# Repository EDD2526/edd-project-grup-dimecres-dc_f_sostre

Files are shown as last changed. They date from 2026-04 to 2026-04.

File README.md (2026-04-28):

# Projecte Eines Sostre Solar 

>**Autors: Nabel Khrourouch i Marc Baillo** 
>**Versió: 0.2 **

----------

## Objectiu

Dissenyar i implementar en una PCB, un sistema electronic del vehicle com es un sostre solar. S’implementara una etapa de regulacio, microcontrolador,  bus CAN, I2C / SPI, USART i botons. 
I que incloguiu les següents caracteristiques:
- Motor del vidre amb el seu final de carrera. 
- Motor de la cortineta.
- Llums ambientals (LED RGB amb bus digital)
- Mecanisme antiatrapament (sensor digital de corrent).

## Diagrama de blocs

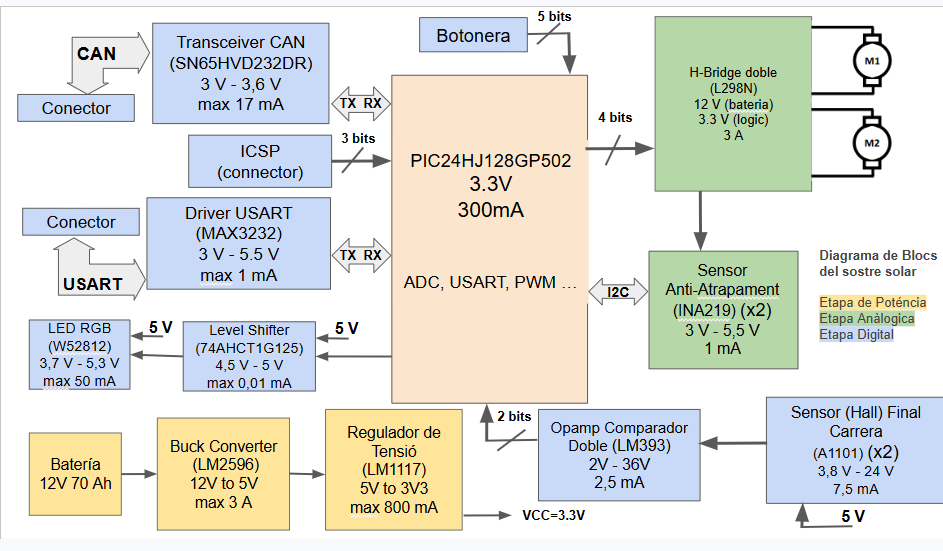
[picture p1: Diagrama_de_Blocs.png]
Diagrama de Bloc


### Descripció/funcionalitat de cada bloc

  * Power: En aquest bloc posem la partt relacionada con 2 etapes, la de la alimentació i la de potencia. (LDO y Buck converter i el H-Bridge)
  * Microcontrolador: en aquest bloc posem les parts que tenen molt que veure amb el microcontrolador com cristal oscilador, ICSP, botonera, filtre pi, reset manual, LEDs de prova.
  * Analógica: part del sistema que és analogic i per tant la agrupem, aquí veiem el sensor de anti-atrapament.
  * Digital: part on están els components més purament digitals, como el USART, el transceiver CAN, el Sensor de Final de Carrera o LED RGB. 

-----------

## Requisits / Especificacions

  * Alimentació; 12V, regulada a 3V3
  * Microcontrolador PIC24hj128gp502
  * Motor del vidre amb el seu final de carrera. 
  * Motor de la cortineta.
  * Llums ambientals (LED RGB amb bus digital)
  * Mecanisme antiatrapament (sensor digital de corrent).

-----------

## Components

| Descripció | Ref | Package | Datasheet | Proveïdor | Preu (per u) | Unitats |
|---|---|---|---|---|---|---|
| Microcontrolador | PIC24HJ128GP502 | TQFP-44 | [Datasheet](https://ww1.microchip.com/downloads/aemDocuments/documents/OTH/ProductDocuments/DataSheets/70293G.pdf) | [Mouser](https://www.mouser.es/ProductDetail/Microchip-Technology/PIC24HJ128GP504-E-PT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) | 6,85€ | 1x |
| Regulador de Tensió | LM1117 | SOT-223 / TO-252-3 | [Datasheet](https://www.ti.com/lit/ds/symlink/lm1117.pdf) | [Mouser](https://www.mouser.es/ProductDetail/Texas-Instruments/LM1117IMPX-3.3-NOPB?qs=X1J7HmVL2ZG7K12CpArCeA%3D%3D) | 0,89€ | 1x |
| Buck Converter (DC/DC) | LM2596 | TO-220-5 | [Datasheet](https://www.onsemi.com/pdf/datasheet/lm2596-d.pdf) | [Mouser](https://www.mouser.es/ProductDetail/onsemi/LM2596DSADJG?qs=atIEnC%2F2K4W1Dy%252BFjrRjIQ%3D%3D) | 2€ | 1x |
| H-Bridge (Doble) | L298N | Multiwatt-15 | [Datasheet](https://www.st.com/resource/en/datasheet/l298.pdf) | [Mouser](https://www.mouser.es/ProductDetail/STMicroelectronics/L298N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) | 9,94€ | 1x |
| Transceiver CAN | SN65HVD232DR | SOIC-8 | [Datasheet](https://www.ti.com/lit/ds/symlink/sn65hvd230.pdf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) | [Mouser](https://eu.mouser.com/ProductDetail/Texas-Instruments/SN65HVD232DR?qs=QViXGNcIEAtY%252BrViRMr46w%3D%3D) | 1,87€  | 1x |
| Driver USART | MAX3232 | SSOP-16 | [Datasheet](https://www.mouser.es/datasheet/3/1014/1/MAX3222-MAX3241.pdf) | [Mouser](https://www.mouser.es/ProductDetail/Analog-Devices-Maxim-Integrated/MAX3232CUE%2bT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) | 6,99€ | 1x |
| Conector | DE9 | DSUB-9_Socket | [Datasheet](https://www.te.com/commerce/DocumentDelivery/DDEController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) | [Mouser](https://www.mouser.es/ProductDetail/TE-Connectivity-AMP/2301843-1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) | 1,9€ | 2x |
| Conector (Batería i Motors) | 282837-2 | THT | [Datasheet](https://www.te.com/commerce/DocumentDelivery/DDEController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) | [Mouser](https://www.mouser.es/ProductDetail/TE-Connectivity/3-282837-2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) | 9,38€ | 3x |
| Sensor (corrent) Anti-Atrapament | INA219 | SOIC-8 | [Datasheet](https://www.ti.com/lit/ds/symlink/ina219.pdf) | [Mouser](https://www.mouser.es/ProductDetail/) | 4,23€ | 2x |
| Sensor Final de Carrera | A1101 | SOT-23 | [Datasheet](https://www.allegromicro.com/~/media/files/datasheets/a110x-datasheet.pdf) | [Mouser](https://www.mouser.es/ProductDetail/Allegro-MicroSystems/A1101EUA-T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) | 1,18€ | 2x |
| Opamp Doble Comparador | LM393 | SOIC-8 | [Datasheet](https://www.ti.com/lit/ds/symlink/lm2903b.pdf?ts=1774335179874&ref_url=https%253A%252F%252Fwww.mouser.pl%252F) | [Mouser](https://www.mouser.es/ProductDetail/Texas-Instruments/LM393AP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) | 0,31 | 1x |
| Cristal Oscilador | ECS-80-20-20BM-EN-TR | 7mm x 5mm | [Datasheet](https://www.mouser.es/datasheet/3/294/1/csm_8mr.pdf) | [Mouser](https://www.mouser.es/ProductDetail/ECS/ECS-80-20-20BM-EN-TR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) | 0,86€ | 1x |
| Ferrita | BLM21 | 0805 | [Datasheet](https://www.mouser.es/datasheet/3/76/1/ENFA0005.pdf) | [Mouser](https://www.mouser.es/ProductDetail/Murata-Electronics/BLM21PG600SN1D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) | 0,10€ | 1x |
| Switch (Pulsador) Reset y Botonera | B3F-1002 | THT | [Datasheet](https://www.mouser.es/datasheet/3/39/1/en_b3f.pdf) | [Mouser](https://www.mouser.es/ProductDetail/Omron-Electronics/B3F-1002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) | 0,27€ | 6x |
| LED blau | LTST-C170TBKT | LED_SMD | [Datasheet](https://www.mouser.com/catalog/specsheets/Lite-On-LTST-C170TBKT.pdf) | [Mouser](https://www.mouser.es/ProductDetail/LITEON/LTST-C170TBKT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) | 0,23€ | 1x |
| LED vermell | LTST-C170KRKT | LED_SMD | [Datasheet](https://www.mouser.com/catalog/specsheets/Lite-On-LTST-C170KRKT.pdf) | [Mouser](https://www.mouser.es/ProductDetail/LITEON/LTST-C170KRKT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) | 0,14€ | 1x |
| LED RGB | WS2812 | LED_SMD | [Datasheet](https://www.tme.eu/Document/01c0100fee68667af99767edc3a7fee2/WS2812B-MINI.pdf) | [TME](https://www.tme.eu/es/details/ws2812b-mini/leds-smd-de-colores/worldsemi/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) | 0,42€ | 1x |
| Level shifter (buffer) | 74AHCT1G125 | SOT-553 | [Datasheet](https://www.ti.com/lit/ds/symlink/sn74ahct1g125.pdf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) | [Mouser](https://www.mouser.es/ProductDetail/Texas-Instruments/74AHCT1G125DBVTG4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) | 0,93€ | 1x |

-----------

## Historial de canvis

| Data | Autor | Branch | Versió | Descripció |
|---|---|---|---|---|
| 10/03/26 | Nabel i Marc | Master | versió 1 | Seleccionem els components i creem la primera versió del Diagrama de Bloc |
| 14/03/26 | Nabel | Master | versió 2 | Actualització del Diagrama de Bloc |
| 16/03/26 | Marc | Master | versió 1 | Esquemàtic: creació dels subapartats del projecte |
| 17/03/26 | Marc | Master | versió 2 | Esquemàtic: faig la part del uC i de Digital |
| 17/03/26 | Nabel | Master | versió 3 | Esquemàtic: faig la part de power i analògica |
| 22/03/26 | Marc | Master | versió 4 | Esquemàtic: correcció d’errades i assignació de footprints |
| 24/03/26 | Nabel | Master | versió 1 | Layout: faig el rutejat de la majoria dels components |
| 24/03/26 | Marc | Master | versió 2 | Layout: corregeixo algunes coses |
| 30/03/26 | Nabel | Master | versió 3 | Layout: rutejat part Digital |
| 31/03/26 | Marc | Master | versió 4 | Layout: treballo part potencia, H_Bridge |
| 08/04/26 | Marc i Nabel | Master | versió 5 | Layout: treballem a classe i l'intentem posar a punt |
| 15/04/26 | Marc i Nabel | Master | versió 6 | Layout: corregim algunes coses com tema de plans i posar plans de massa digital i power |
| 27/04/26 | Nabel | Master | versió 1 | Faig el pressupost |
| 28/04/26 | Marc | Master | versió 7 | Layout: acabo el Layout posant uns canvis proposats pel professor |

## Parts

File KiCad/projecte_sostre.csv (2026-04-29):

Reference | Qty | Value | DNP | Exclude from BOM | Exclude from Board | Footprint | Datasheet
C1,C2,C3,C7,C8,C9,C11,C12,C13,C18,C19,C20,C21,C22,C23,C24,C25,C26,C27,C28,C29,C30,C31,C32,C33,C34,C35,C36,C37,C38 | 30 | 100n |  |  |  | Capacitor_SMD:C_0805_2012Metric | ~
C4,C14,C15,C17 | 4 | 10u |  |  |  | Capacitor_SMD:C_0805_2012Metric | ~
C5,C6 | 2 | 30p |  |  |  | Capacitor_SMD:C_0805_2012Metric | ~
C10 | 1 | 1u |  |  |  | Capacitor_SMD:C_0805_2012Metric | ~
C16 | 1 | 220u |  |  |  | Capacitor_SMD:C_0805_2012Metric | ~
D1,D2 | 2 | LED |  |  |  | LED_SMD:LED_0805_2012Metric | ~
D3,D4 | 2 | 1N5822 |  |  |  | Diode_THT:D_DO-201AD_P15.24mm_Horizontal | http://www.vishay.com/docs/88526/1n5820.pdf
D5 | 1 | WS2812B |  |  |  | LED_SMD:LED_WS2812B_PLCC4_5.0x5.0mm_P3.2mm | https://cdn-shop.adafruit.com/datasheets/WS2812B.pdf
D6,D7,D8,D9,D10,D11,D12,D13 | 8 | D |  |  |  | Diode_SMD:D_SMA | ~
FB1 | 1 | FerriteBead |  |  |  | Resistor_SMD:R_0805_2012Metric | ~
J1,J3,J4,J5,J6 | 5 | Conn_01x02 |  |  |  | Connector_PinHeader_2.54mm:PinHeader_1x02_P2.54mm_Vertical | ~
J2 | 1 | Conn_01x05 |  |  |  | Connector_PinHeader_2.54mm:PinHeader_1x05_P2.54mm_Vertical | ~
J7,J8,J9 | 3 | Screw_Terminal_01x02 |  |  |  | TerminalBlock:TerminalBlock_MaiXu_MX126-5.0-02P_1x02_P5.00mm | ~
J10,J11 | 2 | DE9_Pins |  |  |  | Connector_Dsub:DSUB-9_Pins_Horizontal_P2.77x2.54mm_EdgePinOffset9.40mm | ~
L1 | 1 | 33u |  |  |  | Inductor_SMD:L_1210_3225Metric | ~
R1,R4,R5,R6,R7,R8,R11,R12,R14,R21,R24,R26,R28,R31,R33,R39,R40,R41,R42 | 19 | 10k |  |  |  | Resistor_SMD:R_0805_2012Metric | ~
R2 | 1 | 150 |  |  |  | Resistor_SMD:R_0805_2012Metric | ~
R3,R22,R23 | 3 | 60 |  |  |  | Resistor_SMD:R_0805_2012Metric | ~
R9 | 1 | 3,1k |  |  |  | Resistor_SMD:R_0805_2012Metric | ~
R10 | 1 | 1k |  |  |  | Resistor_SMD:R_0805_2012Metric | ~
R13,R15 | 2 | 3.3k |  |  |  | Resistor_SMD:R_0805_2012Metric | ~
R16,R25 | 2 | 20k |  |  |  | Resistor_SMD:R_0805_2012Metric | ~
R17,R18,R19,R20 | 4 | 50 |  |  |  | Resistor_SMD:R_0805_2012Metric | ~
R27,R29,R30,R32 | 4 | 22k |  |  |  | Resistor_SMD:R_0805_2012Metric | ~
R34,R35,R36,R37 | 4 | 220k |  |  |  | Resistor_SMD:R_0805_2012Metric | ~
R38 | 1 | 330 |  |  |  | Resistor_SMD:R_0805_2012Metric | ~
R43 | 1 | 0 |  |  |  | Resistor_SMD:R_0805_2012Metric | ~
Rshunt1,Rshunt2 | 2 | 0.05 |  |  |  | Resistor_SMD:R_0805_2012Metric | ~
SW1,SW2,SW3,SW4,SW5,SW6 | 6 | SW_Push |  |  |  | Button_Switch_THT:SW_PUSH_6mm | ~
TP_3V3,TP_5V0,TP_GND1,TP_GND2,TP_GND3,TP_GNDPWM1,TP_GNDPWM2,TP_GNDPWM3,TP_GNDPWM4,TP_Vbat0 | 10 | TestPoint |  |  |  | TestPoint:TestPoint_Pad_D1.5mm | ~
TP_PWM_M1,TP_PWM_M2,TP_Rshunt1,TP_Rshunt2,TP_SCL0,TP_SDA0 | 6 | TestPoint_2Pole |  |  |  | TestPoint:TestPoint_2Pads_Pitch2.54mm_Drill0.8mm | ~
U1 | 1 | 74AHCT1G125 |  |  |  | Package_TO_SOT_SMD:SOT-23-5_HandSoldering | http://www.ti.com/lit/sg/scyt129e/scyt129e.pdf
U2,U3 | 2 | LM393 |  |  |  | Package_SO:SOIC-8_3.9x4.9mm_P1.27mm | http://www.ti.com/lit/ds/symlink/lm393.pdf
U4 | 1 | PIC24HJ128GP502 |  |  |  | Package_QFP:TQFP-44_10x10mm_P0.8mm | http://ww1.microchip.com/downloads/en/DeviceDoc/30000684B.pdf
U5 | 1 | LM1117DT-3.3 |  |  |  | Package_TO_SOT_SMD:TO-252-3_TabPin2 | http://www.ti.com/lit/ds/symlink/lm1117.pdf
U6 | 1 | LM2596T-5 |  |  |  | Package_TO_SOT_THT:TO-220-5_P3.4x3.7mm_StaggerOdd_Lead3.8mm_Vertical | http://www.ti.com/lit/ds/symlink/lm2596.pdf
U8,U9 | 2 | INA219AxD |  |  |  | Package_SO:SOIC-8_3.9x4.9mm_P1.27mm | http://www.ti.com/lit/ds/symlink/ina219.pdf
U10 | 1 | MCP2561-E-MF |  |  |  | Package_SO:SOIC-8-1EP_3.9x4.9mm_P1.27mm_EP2.29x3mm | http://ww1.microchip.com/downloads/en/DeviceDoc/25167A.pdf
U11 | 1 | MAX3232 |  |  |  | Package_SO:SOIC-16_3.9x9.9mm_P1.27mm | https://datasheets.maximintegrated.com/en/ds/MAX3222-MAX3241.pdf
U12,U13 | 2 | A1101xLH |  |  |  | Package_TO_SOT_SMD:SOT-23W | https://www.allegromicro.com/-/media/files/datasheets/a110x-datasheet.ashx
U14 | 1 | L298P |  |  |  | Package_SO:Infineon_SOIC-20W_7.6x12.8mm_P1.27mm | http://www.st.com/st-web-ui/static/active/en/resource/technical/document/datasheet/CD00000240.pdf
Y1 | 1 | Crystal |  |  |  | Crystal:Crystal_HC52-6mm_Vertical | ~

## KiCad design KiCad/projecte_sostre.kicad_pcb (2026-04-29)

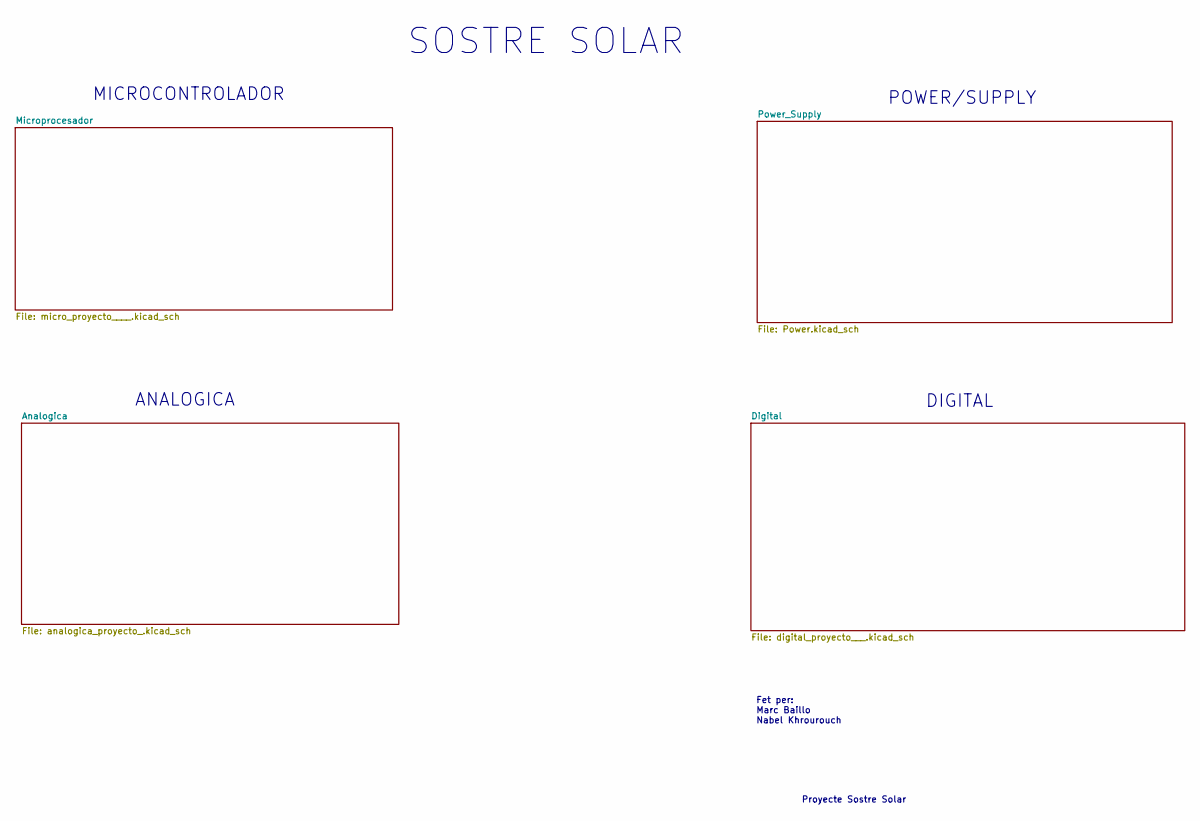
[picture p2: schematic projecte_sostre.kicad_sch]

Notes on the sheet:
SOSTRE SOLAR
Proyecte Sostre Solar
MICROCONTROLADOR
POWER/SUPPLY
ANALOGICA
Fet per: Marc Baillo Nabel Khrourouch
DIGITAL

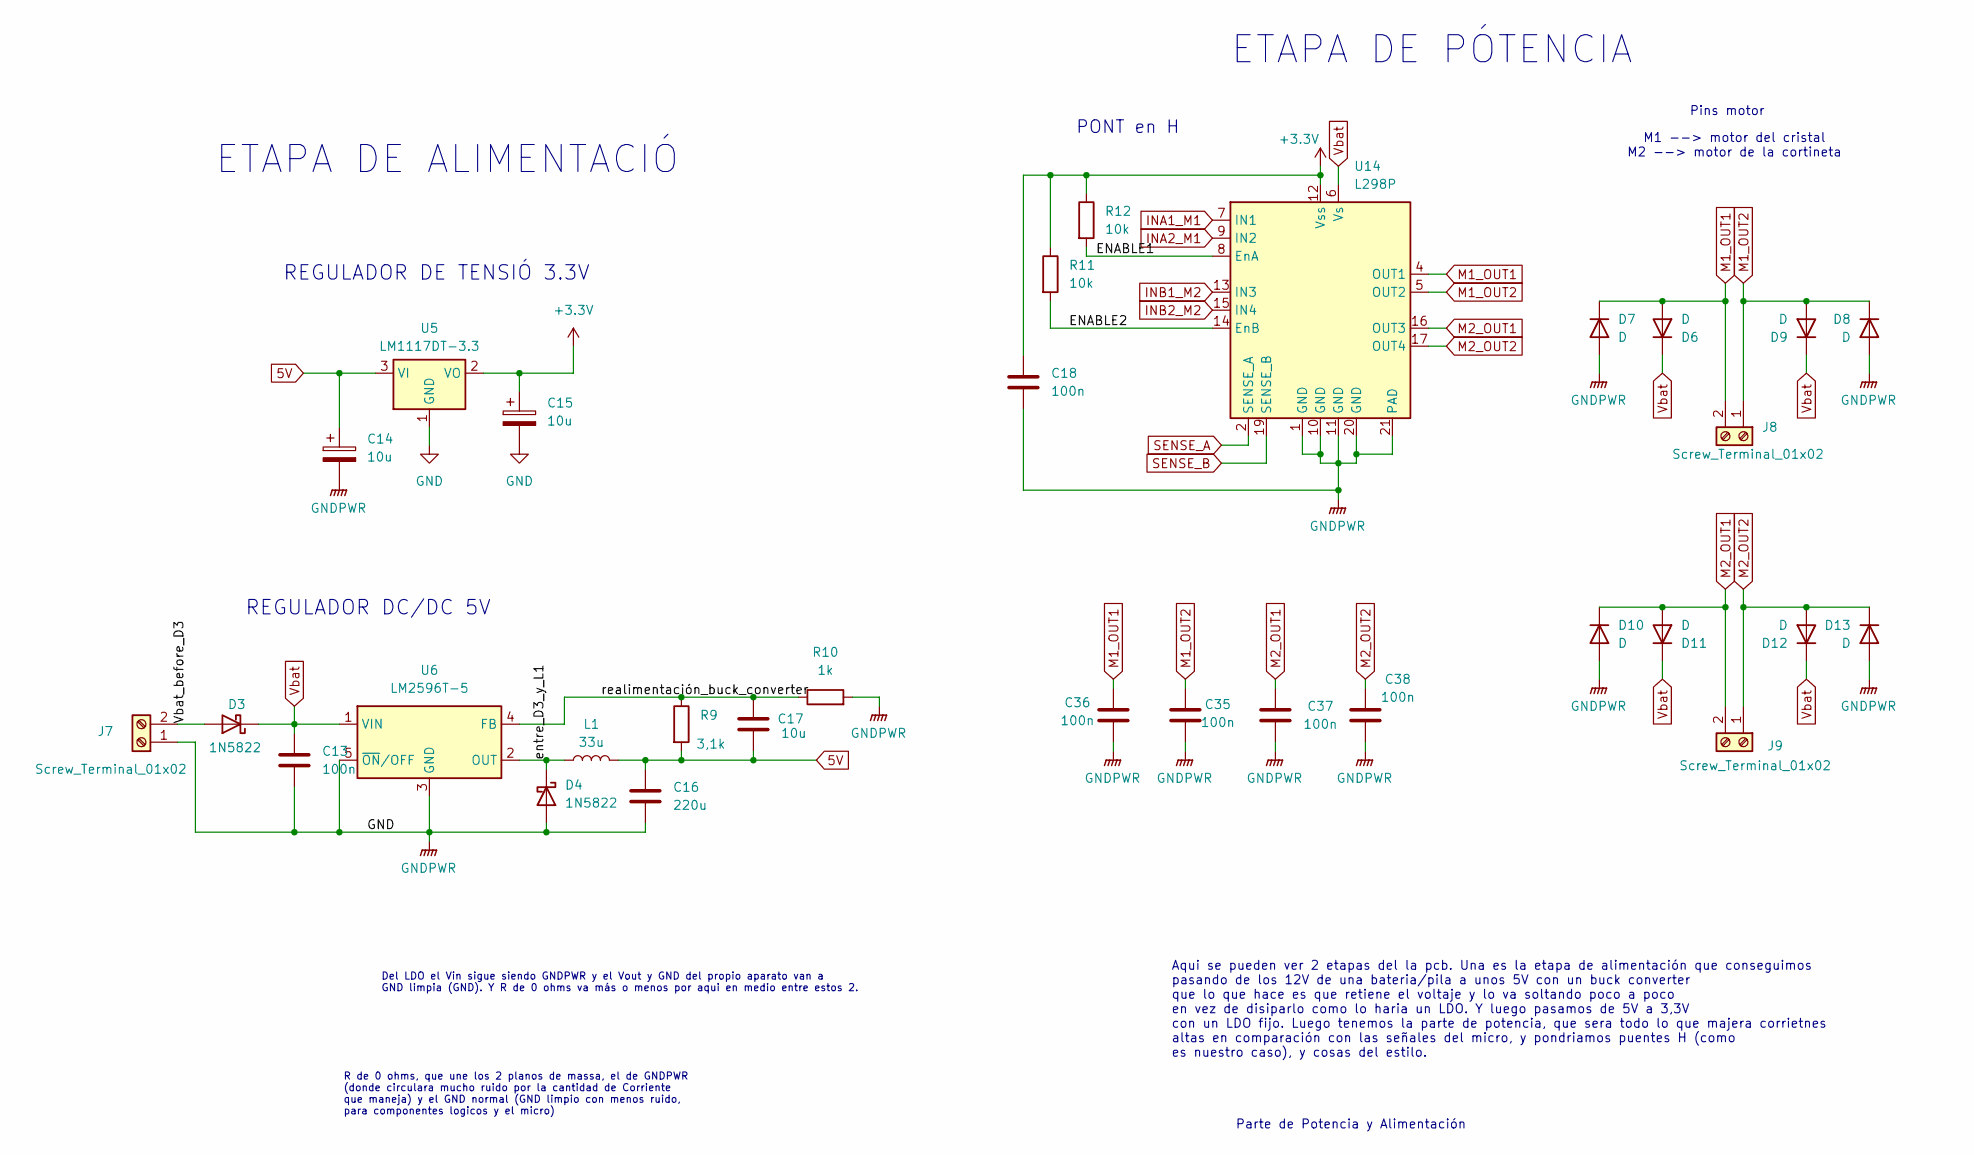
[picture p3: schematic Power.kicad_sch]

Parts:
C13, C18, C35, C36, C37, C38: 100n; C_0805_2012Metric
C14, C15, C17: 10u; C_0805_2012Metric
C16: 220u; C_0805_2012Metric
D3, D4: 1N5822; D_DO-201AD_P15.24mm_Horizontal
D6, D7, D8, D9, D10, D11, D12, D13: D; D_SMA
J7, J8, J9: Screw_Terminal_01x02; TerminalBlock_MaiXu_MX126-5.0-02P_1x02_P5.00mm
L1: 33u; L_1210_3225Metric
R9: 3,1k; R_0805_2012Metric
R10: 1k; R_0805_2012Metric
R11, R12: 10k; R_0805_2012Metric
U5: LM1117DT-3.3; TO-252-3_TabPin2
U6: LM2596T-5; TO-220-5_P3.4x3.7mm_StaggerOdd_Lead3.8mm_Vertical
U14: L298P; Infineon_SOIC-20W_7.6x12.8mm_P1.27mm

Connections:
5V: C14.1, C16.1, C17.2, L1.2, R9.2, U5.3 (VI); also elsewhere on the board
+3.3V: C15.1, C18.1, R11.1, R12.1, U5.2 (VO), U14.12 (Vss); also elsewhere on the board
/Power_Supply/ENABLE1: R12.2, U14.8 (EnA)
/Power_Supply/ENABLE2: R11.2, U14.14 (EnB)
/Power_Supply/Vbat_before_D3: D3.2 (A), J7.2
/Power_Supply/entre_D3_y_L1: D4.1 (K), L1.1, U6.2 (OUT)
/Power_Supply/realimentación_buck_converter: C17.1, R9.1, R10.1, U6.4 (FB)
GND: C13.2, C14.2, C15.2, C16.2, C18.2, C35.2, C36.2, C37.2, C38.2, D4.2 (A), D7.2 (A), D8.2 (A), D10.2 (A), D13.2 (A), J7.1, R10.2, U5.1 (GND), U6.3 (GND), U6.5 (~ON/OFF), U14.1 (GND), U14.10 (GND), U14.11 (GND), U14.20 (GND), U14.21 (PAD); also elsewhere on the board
INA1_M1: U14.7 (IN1); also elsewhere on the board
INA2_M1: U14.9 (IN2); also elsewhere on the board
INB1_M2: U14.13 (IN3); also elsewhere on the board
INB2_M2: U14.15 (IN4); also elsewhere on the board
M1_OUT1: C36.1, D6.2 (A), D7.1 (K), J8.2, U14.4 (OUT1)
M1_OUT2: C35.1, D8.1 (K), D9.2 (A), J8.1, U14.5 (OUT2)
M2_OUT1: C37.1, D10.1 (K), D11.2 (A), J9.2, U14.16 (OUT3)
M2_OUT2: C38.1, D12.2 (A), D13.1 (K), J9.1, U14.17 (OUT4)
SENSE_A: U14.2 (SENSE_A); also elsewhere on the board
SENSE_B: U14.19 (SENSE_B); also elsewhere on the board
Vbat: C13.1, D3.1 (K), D6.1 (K), D9.1 (K), D11.1 (K), D12.1 (K), U6.1 (VIN), U14.6 (Vs); also elsewhere on the board

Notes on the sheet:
Parte de Potencia y Alimentación
PONT en H
R de 0 ohms, que une los 2 planos de massa, el de GNDPWR (donde circulara mucho ruido por la cantidad de Corriente que maneja) y el GND normal (GND limpio con menos ruido, para componentes logicos y el micro)
Aqui se pueden ver 2 etapas del la pcb. Una es la etapa de alimentación que conseguimos pasando de los 12V de una bateria/pila a unos 5V con un buck converter que lo que hace es que retiene el voltaje y lo va soltando poco a poco en vez de disiparlo como lo haria un LDO. Y luego pasamos de 5V a 3,3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
M1 --> motor del cristal M2 --> motor de la cortineta
REGULADOR DC/DC 5V
ETAPA DE PÓTENCIA
ETAPA DE ALIMENTACIÓ
REGULADOR DE TENSIÓ 3.3V
Del LDO el Vin sigue siendo GNDPWR y el Vout y GND del propio aparato van a GND limpia (GND). Y R de 0 ohms va más o menos por aqui en medio entre estos 2.
Pins motor

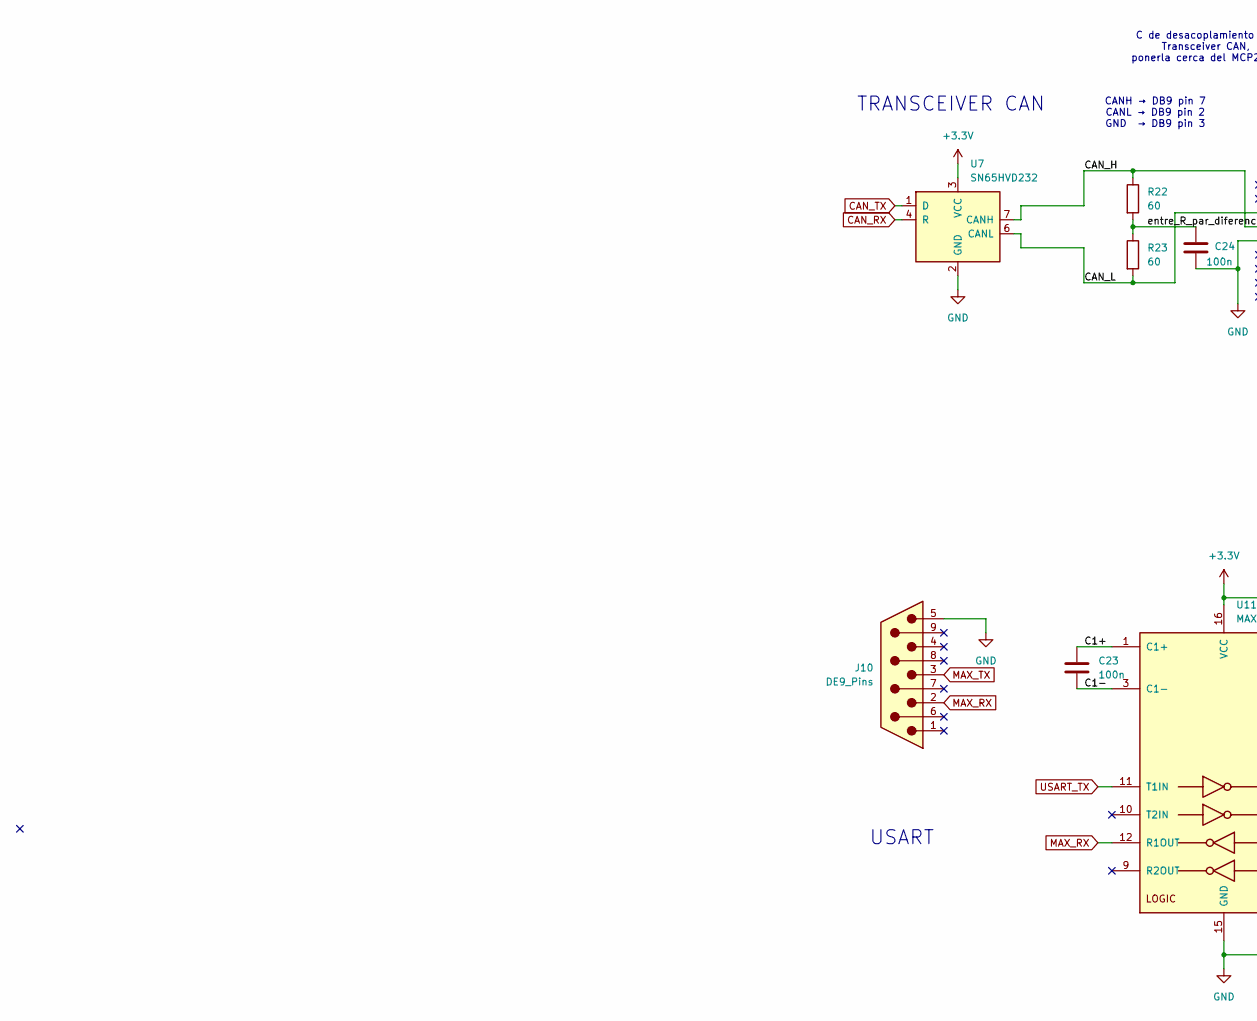
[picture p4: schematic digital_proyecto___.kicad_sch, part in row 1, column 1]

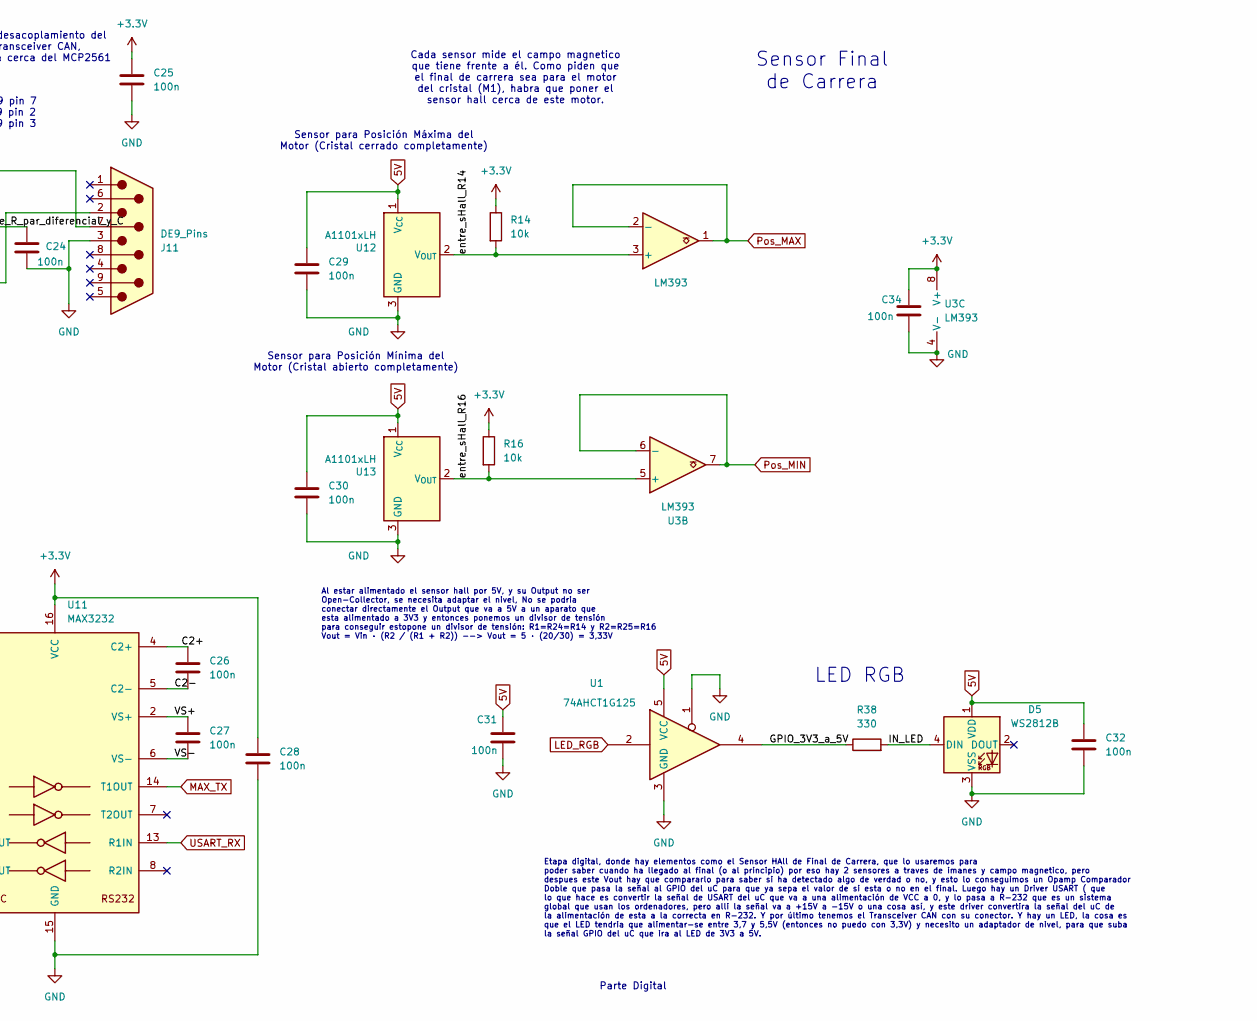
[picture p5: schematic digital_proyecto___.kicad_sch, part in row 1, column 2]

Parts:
C23, C24, C25, C26, C27, C28, C29, C30, C31, C32, C34: 100n; C_0805_2012Metric
D5: WS2812B; LED_WS2812B_PLCC4_5.0x5.0mm_P3.2mm
J10, J11: DE9_Pins; DSUB-9_Pins_Horizontal_P2.77x2.54mm_EdgePinOffset9.40mm
R14, R16: 10k; R_0805_2012Metric
R22, R23: 60; R_0805_2012Metric
R38: 330; R_0805_2012Metric
U1: 74AHCT1G125; SOT-23-5_HandSoldering
U3: LM393; SOIC-8_3.9x4.9mm_P1.27mm
U7: SN65HVD232; SOIC-8_3.9x4.9mm_P1.27mm
U11: MAX3232; SOIC-16_3.9x9.9mm_P1.27mm
U12, U13: A1101xLH; SOT-23W

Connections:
5V: C29.1, C30.1, C31.1, C32.1, D5.1 (VDD), U1.5 (VCC), U12.1 (V_{CC}), U13.1 (V_{CC}); also elsewhere on the board
+3.3V: C25.1, C28.1, C34.1, R14.1, R16.1, U3.8 (V+), U7.3 (VCC), U11.16 (VCC); also elsewhere on the board
/Digital/C1+: C23.1, U11.1 (C1+)
/Digital/C1-: C23.2, U11.3 (C1-)
/Digital/C2+: C26.1, U11.4 (C2+)
/Digital/C2-: C26.2, U11.5 (C2-)
/Digital/CAN_H: J11.7, R22.1, U7.7 (CANH)
/Digital/CAN_L: J11.2, R23.2, U7.6 (CANL)
/Digital/GPIO_3V3_a_5V: R38.1, U1.4
/Digital/IN_LED: D5.4 (DIN), R38.2
/Digital/VS+: C27.1, U11.2 (VS+)
/Digital/VS-: C27.2, U11.6 (VS-)
/Digital/entre_R_par_diferencial_y_C: C24.1, R22.2, R23.1
/Digital/entre_sHall_R14: R14.2, U3.3 (+), U12.2 (V_{OUT})
/Digital/entre_sHall_R16: R16.2, U3.5 (+), U13.2 (V_{OUT})
CAN_RX: U7.4 (R); also elsewhere on the board
CAN_TX: U7.1 (D); also elsewhere on the board
GND: C24.2, C25.2, C28.2, C29.2, C30.2, C31.2, C32.2, C34.2, D5.3 (VSS), J10.5, J11.3, U1.1, U1.3 (GND), U3.4 (V-), U7.2 (GND), U11.15 (GND), U12.3 (GND), U13.3 (GND); also elsewhere on the board
LED_RGB: U1.2; also elsewhere on the board
MAX_RX: J10.2, U11.12 (R1OUT)
MAX_TX: J10.3, U11.14 (T1OUT)
Pos_MAX: U3.1, U3.2 (-); also elsewhere on the board
Pos_MIN: U3.6 (-), U3.7; also elsewhere on the board
USART_RX: U11.13 (R1IN); also elsewhere on the board
USART_TX: U11.11 (T1IN); also elsewhere on the board

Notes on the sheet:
USART
Etapa digital, donde hay elementos como el Sensor HAll de Final de Carrera, que lo usaremos para poder saber cuando ha llegado al final (o al principio) por eso hay 2 sensores a traves de imanes y campo magnetico, pero despues este Vout hay que compararlo para saber si ha detectado algo de verdad o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
Parte Digital
Al estar alimentado el sensor hall por 5V, y su Output no ser Open-Collector, se necesita adaptar el nivel, No se podria conectar directamente el Output que va a 5V a un aparato que esta alimentado a 3V3 y entonces ponemos un divisor de tensión para conseguir estopone un divisor de tensión: R1=R24=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
TRANSCEIVER CAN
Sensor para Posición Mínima del Motor (Cristal abierto completamente)
CANH → DB9 pin 7 CANL → DB9 pin 2 GND → DB9 pin 3
Cada sensor mide el campo magnetico que tiene frente a él. Como piden que el final de carrera sea para el motor del cristal (M1), habra que poner el sensor hall cerca de este motor.
C de desacoplamiento del Transceiver CAN, ponerla cerca del MCP2561
Sensor para Posición Máxima del Motor (Cristal cerrado completamente)
Sensor Final de Carrera
LED RGB

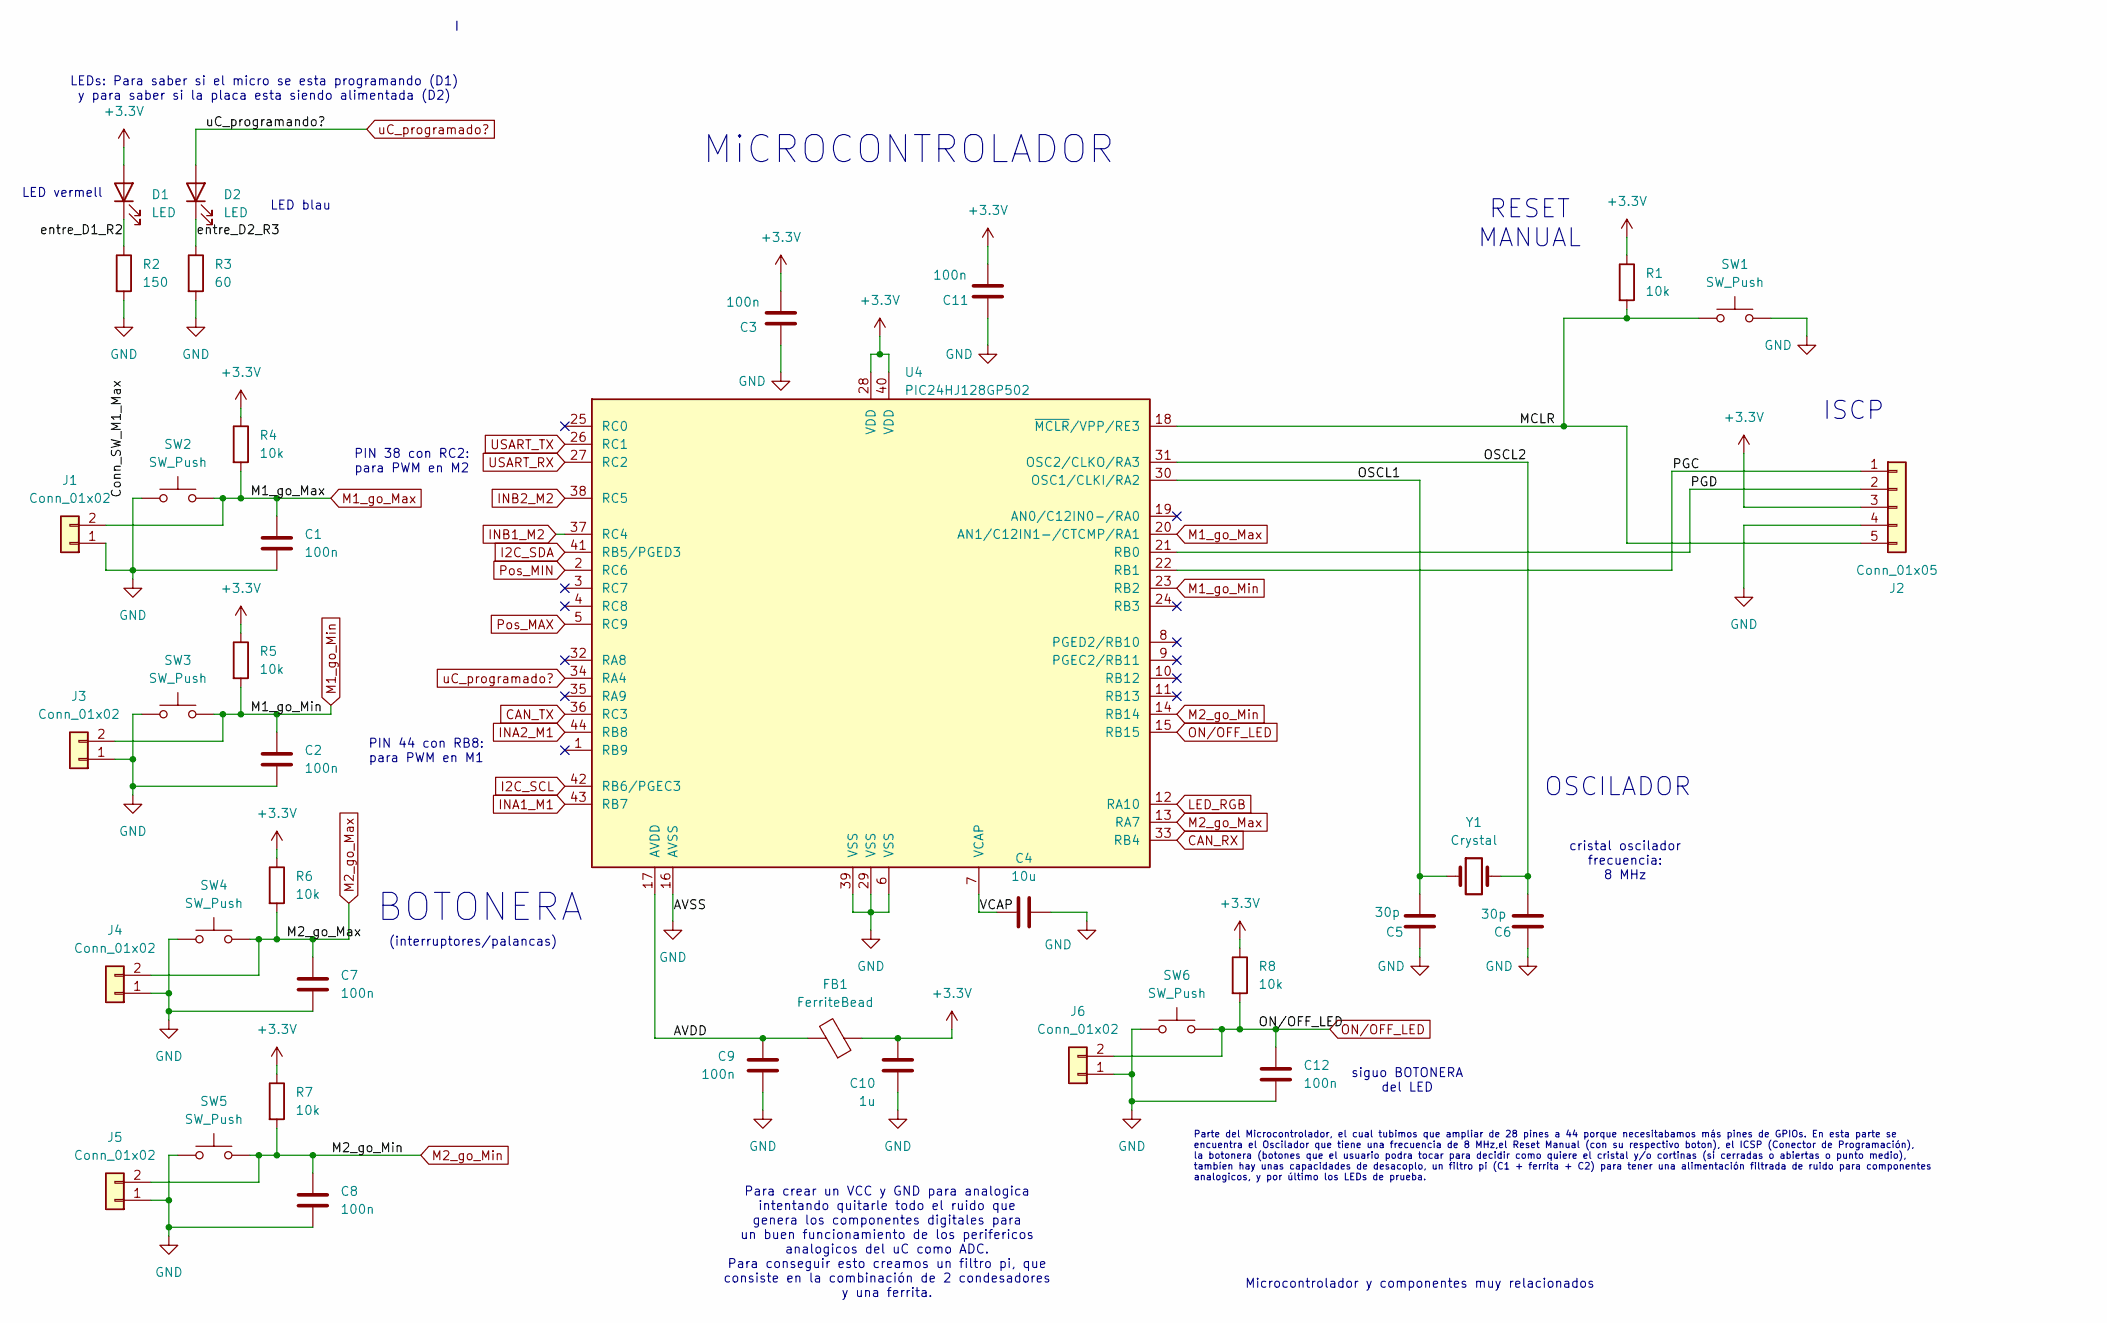
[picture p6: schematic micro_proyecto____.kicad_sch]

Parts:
C1, C2, C3, C7, C8, C9, C11, C12: 100n; C_0805_2012Metric
C4: 10u; C_0805_2012Metric
C5, C6: 30p; C_0805_2012Metric
C10: 1u; C_0805_2012Metric
D1, D2: LED; LED_0805_2012Metric
FB1: FerriteBead; R_0805_2012Metric
J1, J3, J4, J5, J6: Conn_01x02; PinHeader_1x02_P2.54mm_Vertical
J2: Conn_01x05; PinHeader_1x05_P2.54mm_Vertical
R1, R4, R5, R6, R7, R8: 10k; R_0805_2012Metric
R2: 150; R_0805_2012Metric
R3: 60; R_0805_2012Metric
SW1, SW2, SW3, SW4, SW5, SW6: SW_Push; SW_PUSH_6mm
U4: PIC24HJ128GP502; TQFP-44_10x10mm_P0.8mm
Y1: Crystal; Crystal_HC52-6mm_Vertical

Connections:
+3.3V: C3.2, C10.1, C11.2, D1.2 (A), FB1.1, J2.3, R1.1, R4.1, R5.1, R6.1, R7.1, R8.1, U4.28 (VDD), U4.40 (VDD); also elsewhere on the board
/Microprocesador/AVDD: C9.1, FB1.2, U4.17 (AVDD)
/Microprocesador/MCLR: J2.5, R1.2, SW1.1, U4.18 (~MCLR/VPP/RE3)
/Microprocesador/OSCL1: C5.2, U4.30 (OSC1/CLKI/RA2), Y1.1
/Microprocesador/OSCL2: C6.2, U4.31 (OSC2/CLKO/RA3), Y1.2
/Microprocesador/PGC: J2.1, U4.22 (RB1)
/Microprocesador/PGD: J2.2, U4.21 (RB0)
/Microprocesador/VCAP: C4.2, U4.7 (VCAP)
/Microprocesador/entre_D1_R2: D1.1 (K), R2.1
/Microprocesador/entre_D2_R3: D2.1 (K), R3.1
CAN_RX: U4.33 (RB4); also elsewhere on the board
CAN_TX: U4.36 (RC3); also elsewhere on the board
GND: C1.2, C2.2, C3.1, C4.1, C5.1, C6.1, C7.2, C8.2, C9.2, C10.2, C11.1, C12.2, J1.1, J2.4, J3.1, J4.1, J5.1, J6.1, R2.2, R3.2, SW1.2, SW2.1, SW3.1, SW4.1, SW5.1, SW6.1, U4.6 (VSS), U4.16 (AVSS), U4.29 (VSS), U4.39 (VSS); also elsewhere on the board
I2C_SCL: U4.42 (RB6/PGEC3); also elsewhere on the board
I2C_SDA: U4.41 (RB5/PGED3); also elsewhere on the board
INA1_M1: U4.43 (RB7); also elsewhere on the board
INA2_M1: U4.44 (RB8); also elsewhere on the board
INB1_M2: U4.37 (RC4); also elsewhere on the board
INB2_M2: U4.38 (RC5); also elsewhere on the board
LED_RGB: U4.12 (RA10); also elsewhere on the board
M1_go_Max: C1.1, J1.2, R4.2, SW2.2, U4.20 (AN1/C12IN1-/CTCMP/RA1)
M1_go_Min: C2.1, J3.2, R5.2, SW3.2, U4.23 (RB2)
M2_go_Max: C7.1, J4.2, R6.2, SW4.2, U4.13 (RA7)
M2_go_Min: C8.1, J5.2, R7.2, SW5.2, U4.14 (RB14)
ON/OFF_LED: C12.1, J6.2, R8.2, SW6.2, U4.15 (RB15)
Pos_MAX: U4.5 (RC9); also elsewhere on the board
Pos_MIN: U4.2 (RC6); also elsewhere on the board
USART_RX: U4.27 (RC2); also elsewhere on the board
USART_TX: U4.26 (RC1); also elsewhere on the board
uC_programado?: D2.2 (A), U4.34 (RA4)

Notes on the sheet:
MiCROCONTROLADOR
LEDs: Para saber si el micro se esta programando (D1) y para saber si la placa esta siendo alimentada (D2)
LED vermell
Parte del Microcontrolador, el cual tubimos que ampliar de 28 pines a 44 porque necesitabamos más pines de GPIOs. En esta parte se encuentra el Oscilador que tiene una frecuencia de 8 MHz,el Reset Manual (con su respectivo boton), el ICSP (Conector de Programación), la botonera (botones que el usua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
RESET MANUAL
cristal oscilador frecuencia: 8 MHz
ISCP
Para crear un VCC y GND para analogica intentando quitarle todo el ruido que genera los componentes digitales para un buen funcionamiento de los perifericos analogicos del uC como ADC. Para conseguir esto creamos un filtro pi, que consiste en la combinación de 2 condesadores y una ferrita.
Microcontrolador y componentes muy relacionados
OSCILADOR
LED blau
BOTONERA
PIN 38 con RC2: para PWM en M2
PIN 44 con RB8: para PWM en M1
(interruptores/palancas)
siguo BOTONERA del LED

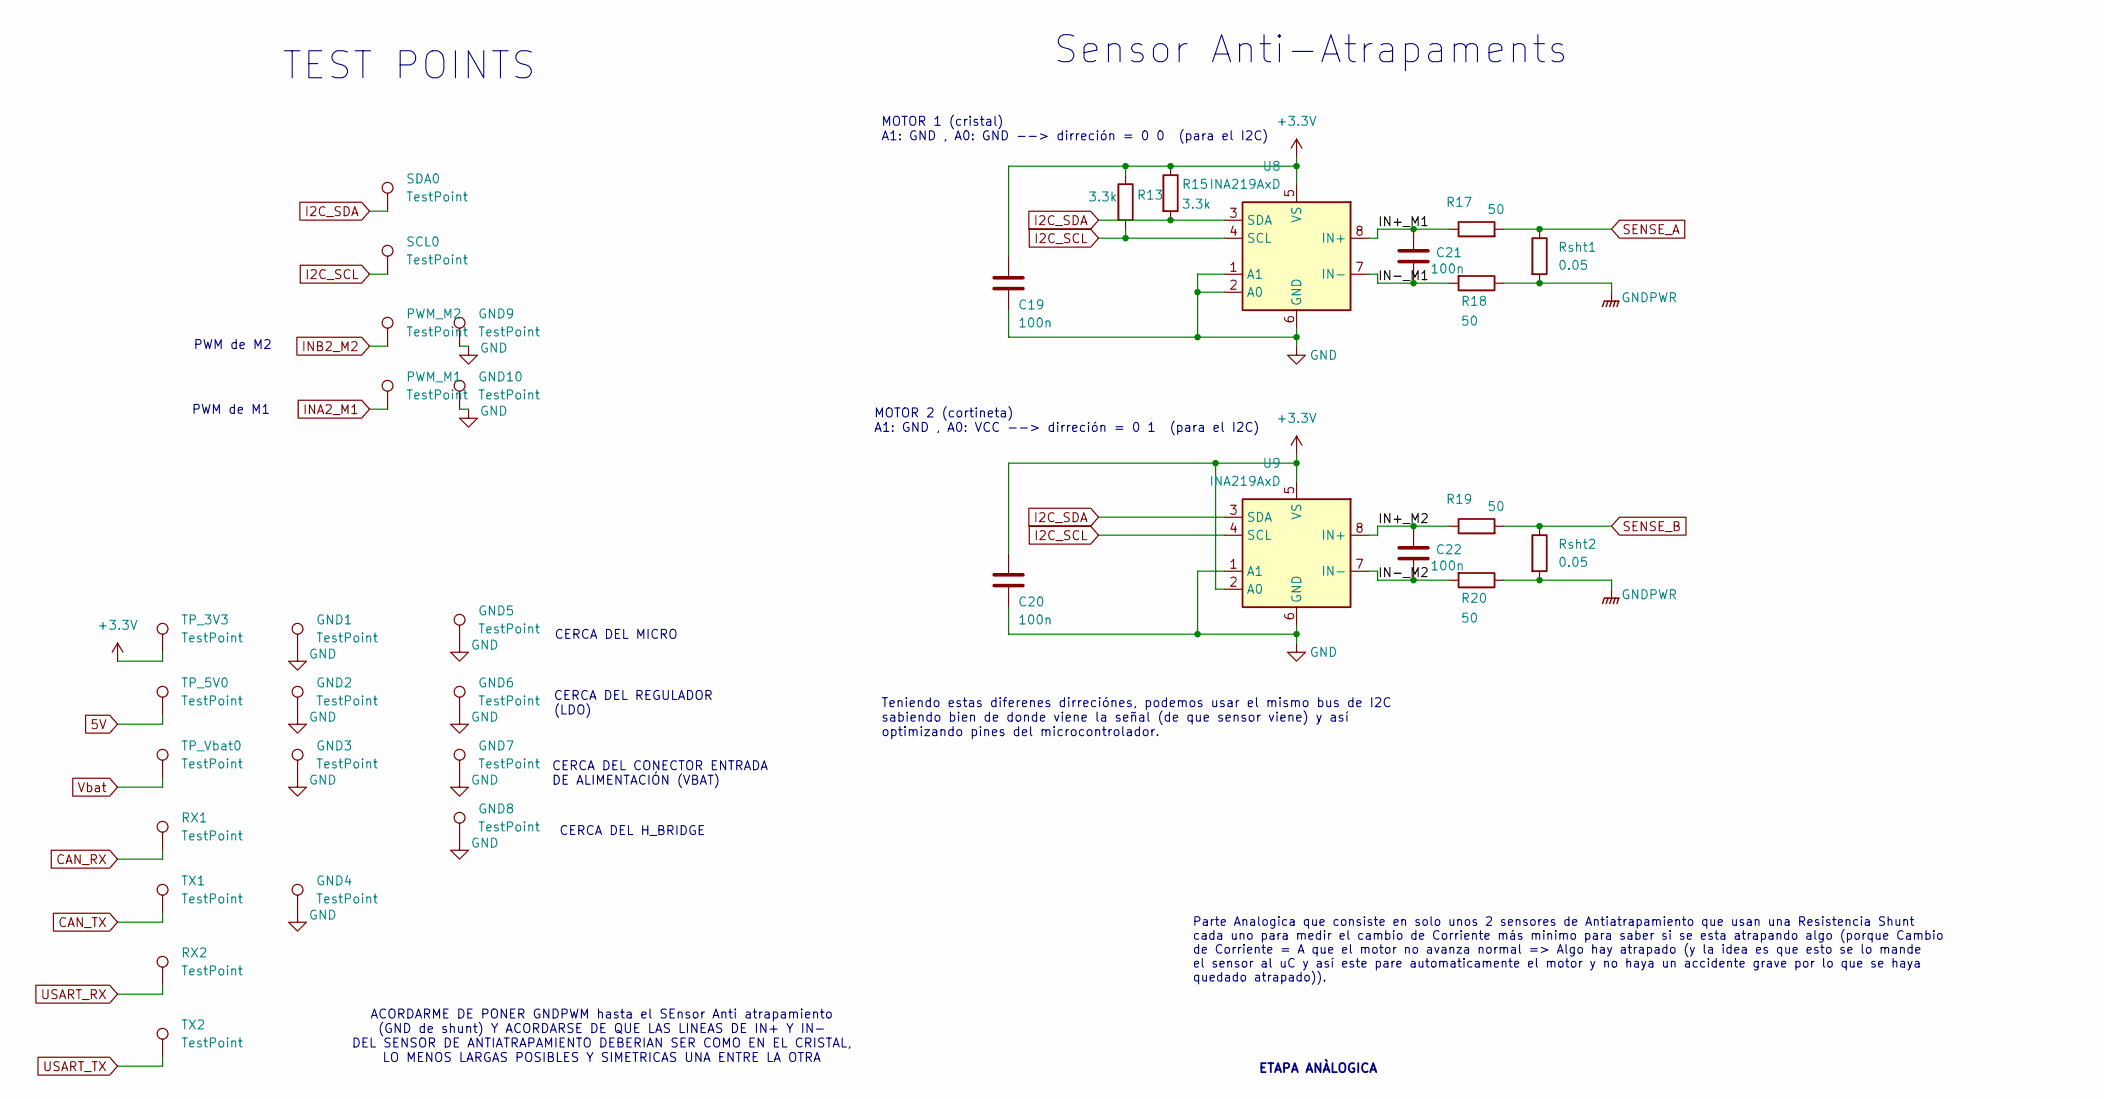
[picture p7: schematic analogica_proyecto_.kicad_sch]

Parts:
C19, C20, C21, C22: 100n; C_0805_2012Metric
GND1, GND2, GND3, GND4, GND5, GND6, GND7, GND8, GND9, GND10: TestPoint; TestPoint_Keystone_5000-5004_Miniature
PWM_M1, PWM_M2: TestPoint; TestPoint_Keystone_5000-5004_Miniature
R13, R15: 3.3k; R_0805_2012Metric
R17, R18, R19, R20: 50; R_0805_2012Metric
RX1, RX2: TestPoint; TestPoint_Keystone_5000-5004_Miniature
Rsht1, Rsht2: 0.05; R_0805_2012Metric
SCL0: TestPoint; TestPoint_Keystone_5000-5004_Miniature
SDA0: TestPoint; TestPoint_Keystone_5000-5004_Miniature
TP_3V3, TP_5V0: TestPoint; TestPoint_Keystone_5000-5004_Miniature
TP_Vbat0: TestPoint; TestPoint_Keystone_5000-5004_Miniature
TX1, TX2: TestPoint; TestPoint_Keystone_5000-5004_Miniature
U8, U9: INA219AxD; SOIC-8_3.9x4.9mm_P1.27mm

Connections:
5V: TP_5V0.1; also elsewhere on the board
+3.3V: C19.1, C20.1, R13.1, R15.1, TP_3V3.1, U8.5 (VS), U9.2 (A0), U9.5 (VS); also elsewhere on the board
/Analogica/IN+_M1: C21.1, R17.1, U8.8 (IN+)
/Analogica/IN+_M2: C22.1, R19.1, U9.8 (IN+)
/Analogica/IN-_M1: C21.2, R18.2, U8.7 (IN-)
/Analogica/IN-_M2: C22.2, R20.2, U9.7 (IN-)
CAN_RX: RX1.1; also elsewhere on the board
CAN_TX: TX1.1; also elsewhere on the board
GND: C19.2, C20.2, GND1.1, GND2.1, GND3.1, GND4.1, GND5.1, GND6.1, GND7.1, GND8.1, GND9.1, GND10.1, R18.1, R20.1, Rsht1.2, Rsht2.2, U8.1 (A1), U8.2 (A0), U8.6 (GND), U9.1 (A1), U9.6 (GND); also elsewhere on the board
I2C_SCL: R13.2, SCL0.1, U8.4 (SCL), U9.4 (SCL); also elsewhere on the board
I2C_SDA: R15.2, SDA0.1, U8.3 (SDA), U9.3 (SDA); also elsewhere on the board
INA2_M1: PWM_M1.1; also elsewhere on the board
INB2_M2: PWM_M2.1; also elsewhere on the board
SENSE_A: R17.2, Rsht1.1; also elsewhere on the board
SENSE_B: R19.2, Rsht2.1; also elsewhere on the board
USART_RX: RX2.1; also elsewhere on the board
USART_TX: TX2.1; also elsewhere on the board
Vbat: TP_Vbat0.1; also elsewhere on the board

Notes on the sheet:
Sensor Anti-Atrapaments
CERCA DEL CONECTOR ENTRADA DE ALIMENTACIÓN (VBAT)
PWM de M2
Teniendo estas diferenes dirreciónes, podemos usar el mismo bus de I2C sabiendo bien de donde viene la señal (de que sensor viene) y así optimizando pines del microcontrolador.
ETAPA ANÀLOGICA
MOTOR 1 (cristal) A1: GND , A0: GND --> dirreción = 0 0 (para el I2C)
PWM de M1
ACORDARME DE PONER GNDPWM hasta el SEnsor Anti atrapamiento (GND de shunt) Y ACORDARSE DE QUE LAS LINEAS DE IN+ Y IN- DEL SENSOR DE ANTIATRAPAMIENTO DEBERIAN SER COMO EN EL CRISTAL, LO MENOS LARGAS POSIBLES Y SIMETRICAS UNA ENTRE LA OTRA
CERCA DEL H_BRIDGE
Parte Analogica que consiste en solo unos 2 sensores de Antiatrapamiento que usan una Resistencia Shunt cada uno para medir el cambio de Corriente más minimo para saber si se esta atrapando algo (porque Cambio de Corriente = A que el motor no avanza normal => Algo hay atrapado (y la idea es que est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
MOTOR 2 (cortineta) A1: GND , A0: VCC --> dirreción = 0 1 (para el I2C)
CERCA DEL REGULADOR (LDO)
CERCA DEL MICRO
TEST POINTS

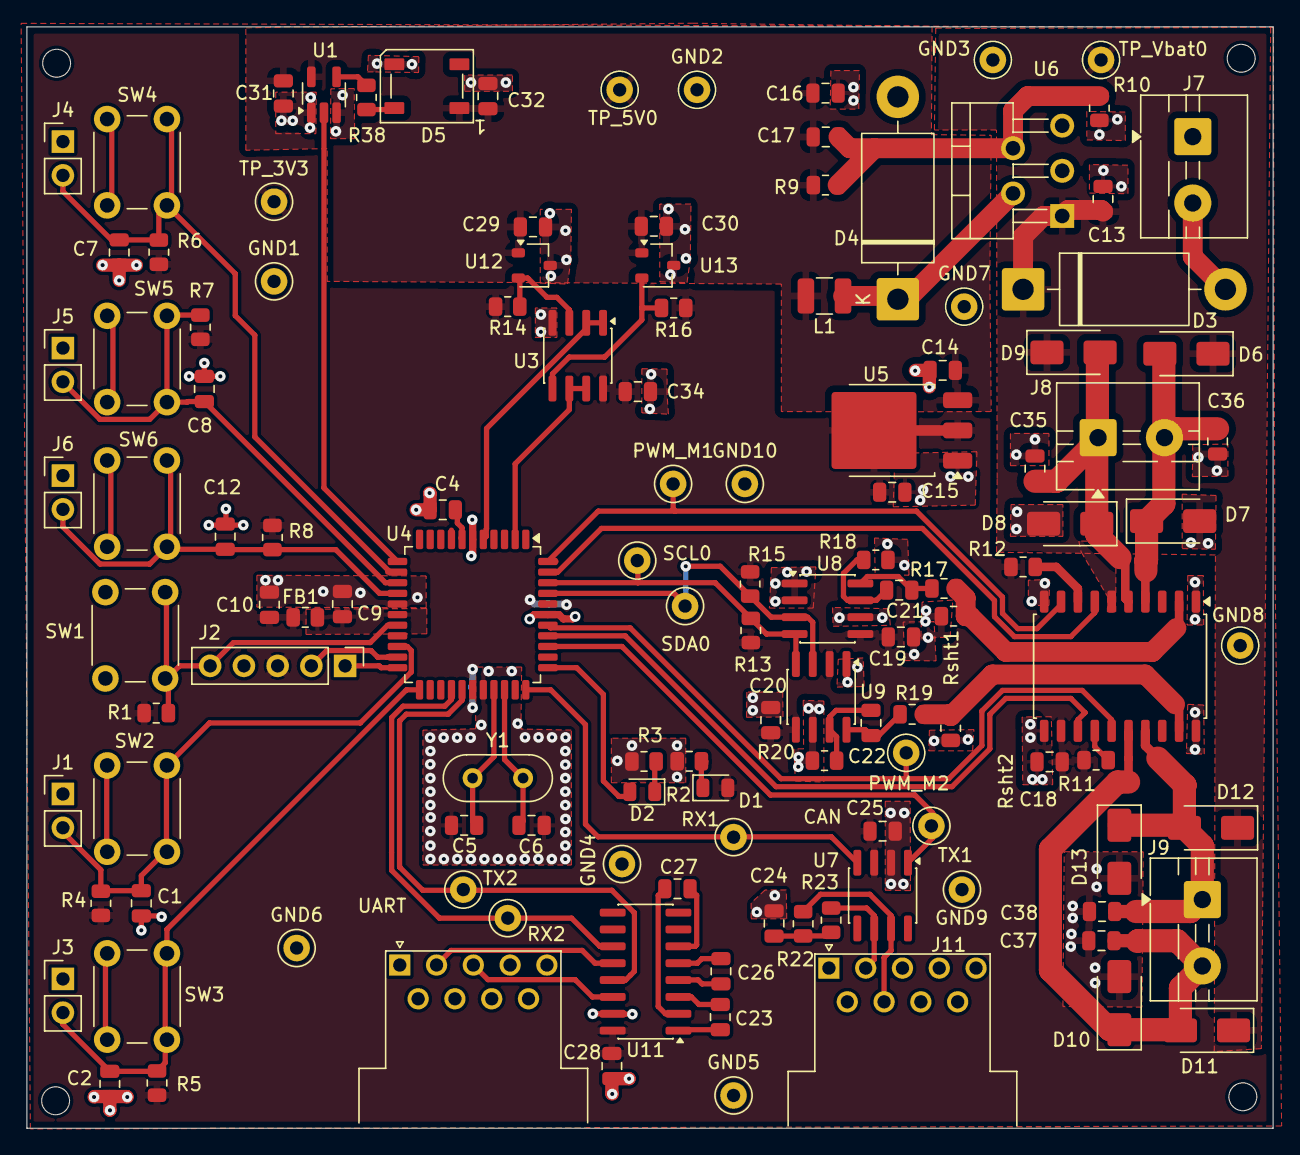
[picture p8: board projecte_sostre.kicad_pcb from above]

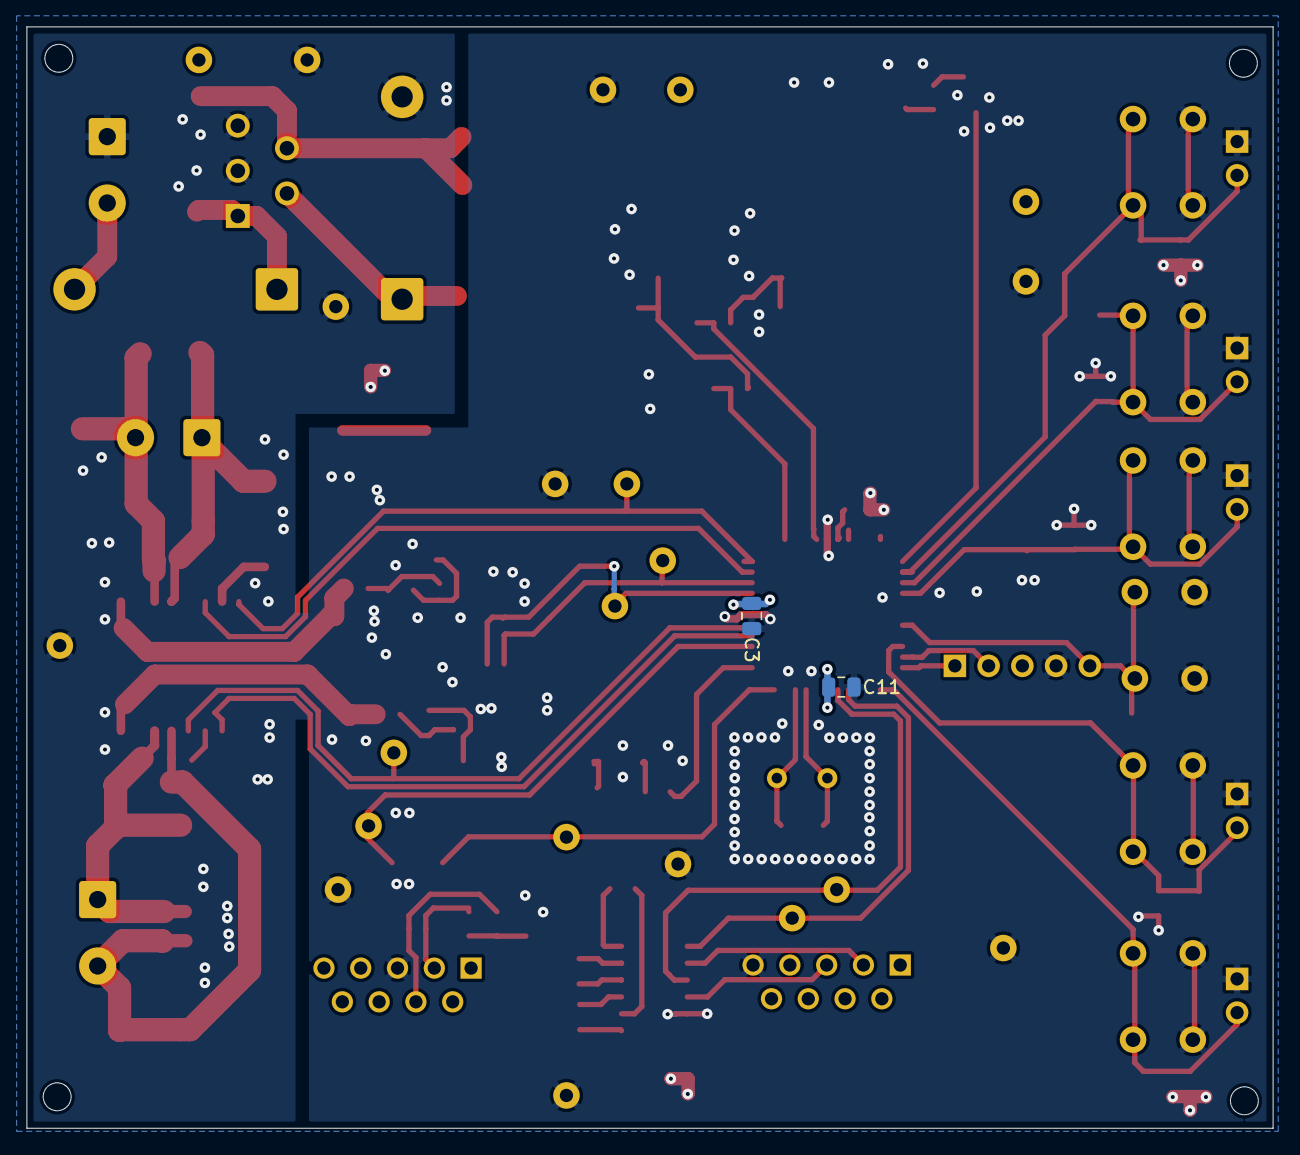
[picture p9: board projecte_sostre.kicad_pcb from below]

Board: 2 copper layers, 93.8 x 82.9 mm, 128 parts (2 on the bottom side), 62 nets.

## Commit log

2026-03-11 projecte kicad creat
    [projecte_sostre.kicad_pcb]
2026-03-11 kicad creat
    [projecte_sostre.kicad_sch]
2026-03-11 esquematic modificat
    [projecte_sostre.kicad_sch]
2026-03-17 Començada part de micro i separacio de les 4 fases o grans grups de la PCB
    [Power.kicad_sch, analogica_proyecto_.kicad_sch, digital_proyecto___.kicad_sch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]
2026-03-18 he afegit la part de potencia
    [Power.kicad_sch]
2026-03-18 afegit part analogica
    [Power.kicad_sch, analogica_proyecto_.kicad_sch, micro_proyecto____.kicad_sch]
2026-03-18 Poner parte digital
    [digital_proyecto___.kicad_sch, micro_proyecto____.kicad_sch]
2026-03-18 Subida para juntarlo todo 100 por 100
    [Power.kicad_sch, digital_proyecto___.kicad_sch, micro_proyecto____.kicad_sch]
2026-03-18 Prueba 1
    [projecte_sostre.kicad_sch]
2026-03-23 Actualización ESquematico arreglandolo y corrigiendo fallos
    [Power.kicad_sch, analogica_proyecto_.kicad_sch, digital_proyecto___.kicad_sch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]
2026-03-23 Nuevos cambios esquemativo v3
    [Power.kicad_sch, analogica_proyecto_.kicad_sch, digital_proyecto___.kicad_sch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]
2026-03-24 Actualización de Esquematico, he puesto footprints y readme cambiado
    [Power.kicad_sch, analogica_proyecto_.kicad_sch, digital_proyecto___.kicad_sch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]
2026-03-24 Añado el Readme
2026-03-24 Esquematico cambio en Sensor final de Carrera y Readme
    [digital_proyecto___.kicad_sch, micro_proyecto____.kicad_sch]
2026-03-24 Esquematico acabado y readme estructura base y componentes acabado y puesto el DB.
    [analogica_proyecto_.kicad_sch, digital_proyecto___.kicad_sch, micro_proyecto____.kicad_sch]
2026-03-24 DG que se vea bien
2026-03-25 layout primer fet, queda canviar coses, pero una primera idea
    [projecte_sostre.kicad_pcb]
2026-03-25 Cambios al esquematico por SEsión 3
    [Power.kicad_sch, analogica_proyecto_.kicad_sch, digital_proyecto___.kicad_sch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]
2026-04-07 Cambio DG y pinzeladas ultimas al esquematico
    [digital_proyecto___.kicad_sch, micro_proyecto____.kicad_sch]
2026-04-09 pujo el esquematico a medio hacer despues de hacer cambios para mejorar el 2o layout
    [Power.kicad_sch, analogica_proyecto_.kicad_sch, digital_proyecto___.kicad_sch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]
2026-04-13 Test Points y Parte POwer ruteada de nuevo
    [Power.kicad_sch, analogica_proyecto_.kicad_sch, projecte_sostre.kicad_pcb]
2026-04-13 Voy a intentar mejorar el LED, sensor hall / sensor antiatrapamiento
    [projecte_sostre.kicad_pcb]
2026-04-13 ultimos cambios, he puesto abajo sensor anti atrapamiento (usa AVDD y SENSOR_A y _B PROBLEMA porque atraviesa todo una linea muy ancha
    [projecte_sostre.kicad_pcb]
2026-04-14 Sensor Hall y LED mas o menos definitivos
    [Power.kicad_sch, analogica_proyecto_.kicad_sch, digital_proyecto___.kicad_sch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]
2026-04-20 Layout con pocos cables en capa Bot pero todavai hay que hacer cambios que nos dijo el Miercoles pasado
    [analogica_proyecto_.kicad_sch, micro_proyecto____.kicad_sch, projecte_sostre.kicad_pcb]
2026-04-26 Cambios Layout propuestos para mejorar posicionamiento
    [analogica_proyecto_.kicad_sch, digital_proyecto___.kicad_sch, micro_proyecto____.kicad_sch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]
2026-04-27 Arreglo de algunos fallos DRC
    [micro_proyecto____.kicad_sch, projecte_sostre.kicad_pcb]
2026-04-28 PCB casi acabada, despues de revisión de ayer 27/04 y cambio en componente CAN, que se vera reflejado en README y en DB
    [Power.kicad_sch, analogica_proyecto_.kicad_sch, digital_proyecto___.kicad_sch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]
2026-04-28 Layout definitivo
    [analogica_proyecto_.kicad_sch, digital_proyecto___.kicad_sch, micro_proyecto____.kicad_sch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]
2026-04-28 Readme definitivo, correción de fallo de escritura y ahora DB si que se ve bien
2026-04-28 Readme ahora si que si deberia estar bien
2026-04-29 layout final
    [projecte_sostre.csv, projecte_sostre.kicad_pcb]
